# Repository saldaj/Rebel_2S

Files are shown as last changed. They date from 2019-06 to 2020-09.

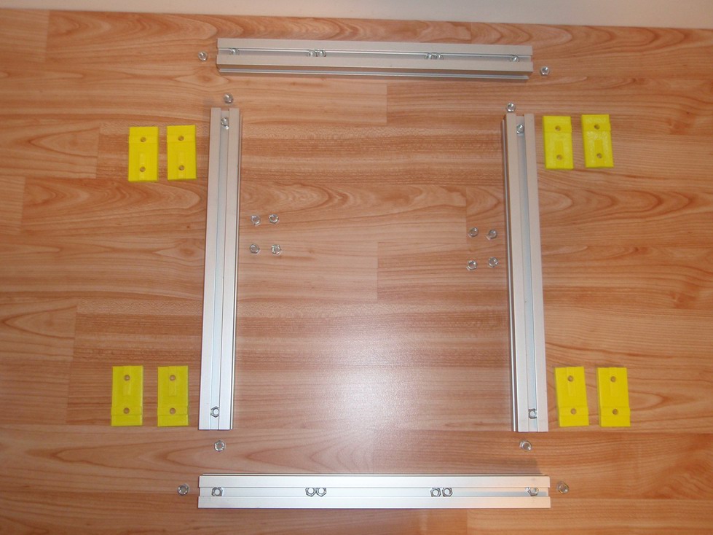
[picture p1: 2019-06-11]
Stavba/NavodyNaStavbu/rebel2-foto-montaz/001-priprava slozeni ramu.JPG

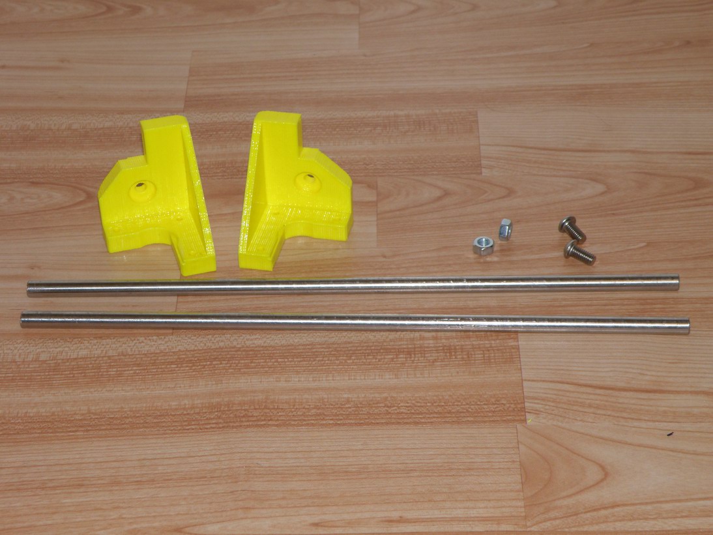
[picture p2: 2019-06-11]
Stavba/NavodyNaStavbu/rebel2-foto-montaz/018-priprava uchyceni Z motoru.JPG

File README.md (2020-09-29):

# Rebel_2S
This is the tracking place for build documents of one 3D printer - Based on the Rebel II printer

Jedna se o 3D tiskarnu Rebel II, ktera byla smontovana na zaklade dostupnych tipu a manualu. Vetsinu materialu se pokusim sem umistit, aby bylo vse pohromade.

Hlavni duvod proc toto vytvarim je FW - marlin, ktery jsem si musel upravit dle svych pozadavku, ale mezi verzemi jsem se zacal ztracet. Proto git je nejlepsi misto, kam dat FW aby byl trackovatelny hlavne vuci zmenam.

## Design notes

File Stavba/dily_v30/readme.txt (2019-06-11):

09:38 17/03/2015
k dispozici jsou dva totozne zdroje pro tisteni dilu:
A) Tistene dily rebel ii_v30_JRC
B) nebo \Stl_Tisk_v30\Sestavy_STL

- obe verze jsou aktualni.

tyto dve slozky se lisi par vecmi:
1. A) ma o 3 4 dily navic
	-Fan_mount_V5.4
	-Fan_mount_V8b
	-Full_g_LCD_vrchni
	-uchytkabelu.stl

2. B) ma moznost tisknout dily v sestave - uspora casu

Doporuèené minimální paranetry tisku:

- Steny/dna/vrchní výplne 1,2mm
- vnitrní výplne 25%

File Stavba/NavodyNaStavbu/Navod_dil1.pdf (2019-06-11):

## Postup stavby 3D tiskárny Rebel II

Martin Čihák – OK1UGA
Díl první - mechanika tiskárny.

Postup se týká stavby tiskárny Rebel II ze sady dílů zakoupené u Petra Zahradníka: http://www.clexpert.cz/3dtisk/rebel2/kompletni-sada-dilu
Je popisován postup který jsem použil při sestavení této tiskárny. V žádném případě netvrdím že je to postup jediný nebo nejlepší. Takto jsem to prostě udělal já a funguje to. Mě při stavbě velmi chyběl alespoň stručný návod a proto jsem ho napsal. Návod je napsán ve formě jednotlivých kroků kterými je potřeba při stavbě projít.
1. Vybalení hliníkových profilů
2. Vybalení pytlíku č. 3. Uvnitř je 52 matek. Ty je potřeba zbrousit asi o 0,3mm tak aby se vešly dovnitř profilů.
3. Nejkratší profily 320 mm jsou spodní boční, tedy vlevo a vpravo.
3.1. Do každého z nich nasadíte:
- zleva 2 matice doprostřed pro úhelník
- zprava 2 matice doprostřed pro úhelník
- nahoru 2 matice na každou stranu pro plastové vazby rohů
- dolu 2 matice na každou stranu pro plastové vazby rohů
To je tedy 2 profily krát 8 matic = 16 matic
3.2. Nejdelší profily 340 mm jsou přední, zadní a horní. Takže do těch spodních dvou nasadíte:
- nahoru 4 matice doprostřed pro držáky 8 mm vodících tyčí
- a nahoru ještě 2 matice na každou stranu pro plastové vazby rohů
- dolů 2 matice na každou stranu pro plastové vazby rohů
To je tedy 2 profily krát 8 matic = 16 matic
Tohle je tedy spodní část rámu, celkem 24 + 16 = 40 matic, tohle smontujete. Pak budete dělat svislé tyče.
3.3. Prostřední profily 330 mm jsou svislé, tam to bude takto:
- zleva 2 matice dolů pro úhelník
- zprava 2 matice dolů pro úhelník
- zpředu 1 matice dolů pro držák motoru
- zpředu 1 matice nahoru pro držák svislé tyče
- zezadu 1 matice nahoru pro vazbu rohů
To je tedy 2 profily krát 7 matic = 14 matic. Ale pozor, do levého svislého profilu zezadu přidejte ještě 2 matice doprostřed pro elektroniku. Celkem 16 matic.
3.4. Horní profil je zase ten nejdelší 340 mm a tam patří
- zpředu 2 matice na každou stranu pro vazbu rohů
- zezadu 2 matice na každou stranu pro vazbu rohů
To jsou celkem 4 matice. A jsme na těch 52 maticích.

Doporučuji do svislých profilů ještě přidat několik matic pro případné budoucí použití - např. pro držák zdroje a podobně. Tyto matky navíc ničemu nevadí a pokud bychom v budoucnu chtěli na tyto sloupky něco připevnit nemusíme rozebírat velkou část postavené tiskárny.

4. Vybalíme plastové díly z pytlíku č.4 - vazba rohů a smontujeme spodní rám. Šrouby na vazby rohů jsou v pytlíku č.5 - Vazba rohů.

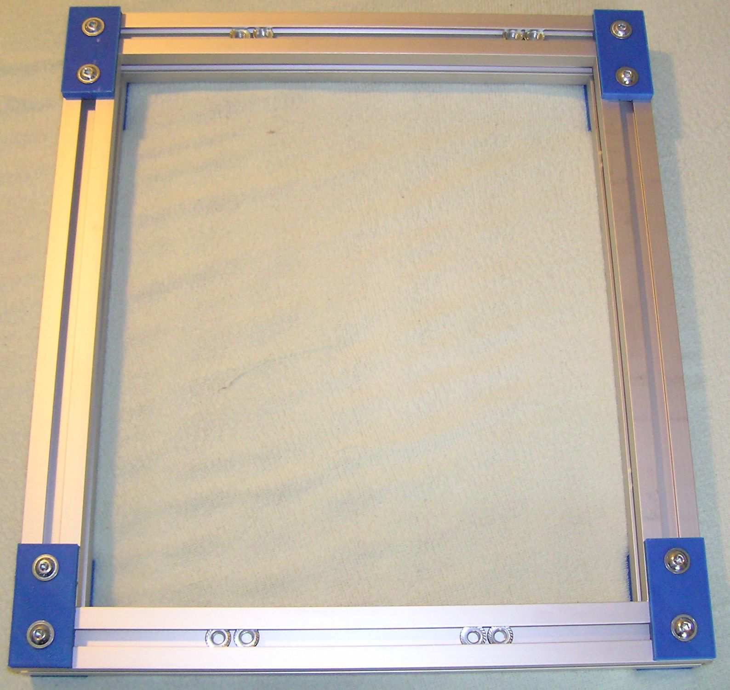
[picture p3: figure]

5. Sestavíme portál. Nejprve na svislé profily našroubujeme připevňovací úhelníky. Zatím utahujeme jen zlehka aby při manipulaci neupadly. Přišroubujeme horní profil. Zezadu je přišroubován posledními spojkami rohů, sepředu jsou profily spojeny držáky tyčí Z které jsou v pytlíku 20. K přišroubování použijeme šrouby z pytlíku 21. Do svislých profilů osadíme zbývající matky - viz odstavec 3.4 a sešroubovaný portál nasadíme na základní rám. Odměříme 100mm od zadní strany spodního rámu a v této poloze portál zlehka přitáhneme. Teď je dobré zkontrolovat pravý úhel mezi základním rámem a svislými profily. pokud je vše v pořádku přitáhněte upevňovací šrouby. Po zkontrolování pravého úhlu a vzdálenosti od konce je základní rám tiskárny sestavený.

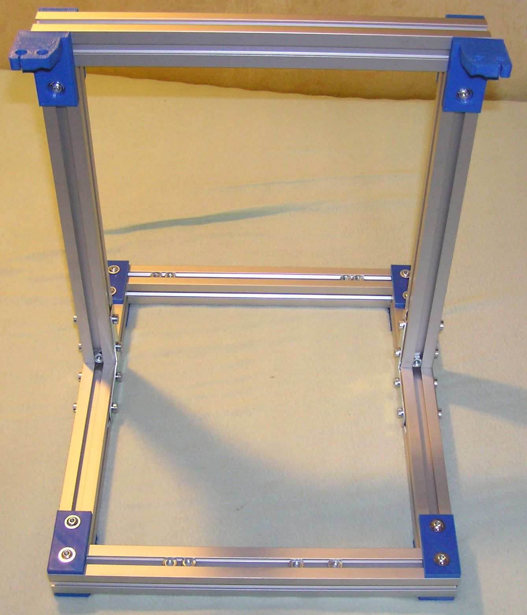
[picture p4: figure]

6. Pokračujeme montáží osy Y.

7. Vybalíme hliníkový stolek tiskárny z pytlíku 38. Z pytlíku 10 vybalíme držáky lineárních ložisek a nastrčíme do nich lineární ložiska z pytlíku 11. Sestavené držáky s ložisky přišroubujeme ke stolku. Našroubujeme z druhé strany kontramatky ale zatím neutahujeme. U držáků lineárních ložisek ale doporučuji nejprve zbrousit do roviny. případné nerovnosti dosedací plochy. Ty mohou způsobit při dotažení prohnutí držáků a vypadnutí ložiska.
8. Z pytlíku 30 vybalíme základnu držáku řemene osy Y a přišroubujeme ho na stolek šrouby z pytlíku 31. Další 2 díly z pytlíku 30 a zbytek šroubů si prozatím uložíme.

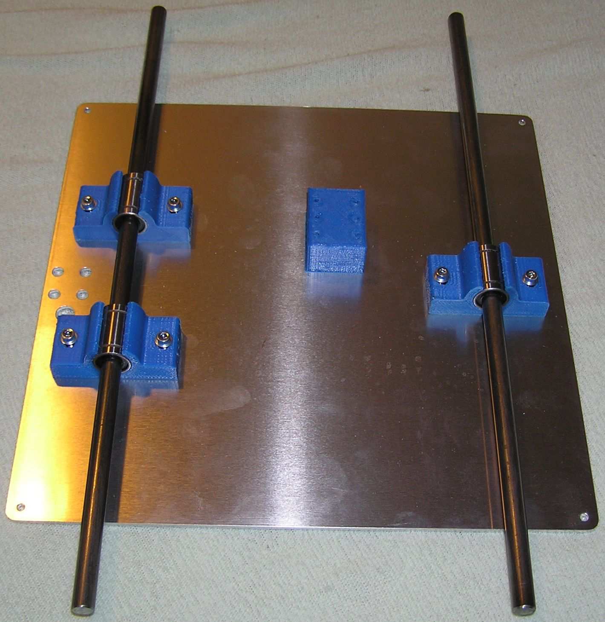
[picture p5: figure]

9. Vybalíme vodící a závitové tyče. Vybereme z nich vodící tyče osy Y - mají délku 365mm a nasuneme je do lineárních ložisek. Domky ložisek přitom jemně natočíme tak aby tyče v ložiscích hladce běhaly a byly rovnoběžné s hranou stolku. Rovnoběžnost kontrolujeme šuplérou.
10. Vybalíme 2kusy uchycení tyčí 8mm z pytlíčku č 6 a přišroubujeme je na předek základního rámu šrouby z pytlíku č.7. Zatím šrouby ale nebudeme dotahovat. Nastavíme vzdálenost předního pravého držáku tyče na 55mm od hrany rámu a utáhneme ho v této poloze. Vysuneme tyče z ložisek stolku a namažeme vnitřek ložisek přiloženým plastickým mazivem. Pak vrátíme tyče zpět do ložisek. Pravou tyč zasuneme do zafixovaného držáku a levý držák posuneme tak aby do něj šla zasunout levá tyč. Zezadu na tyče nasuneme zbývající 2 držáky a přichytíme je k rámu. Pravý zadní držák zafixujeme rovněž ve vzdálenosti 55mm od hrany rámu. Posunujeme stolkem dopředu a dozadu a 2 nezafixované držáky nastavíme do takové polohy aby stolek hladce klouzal po tyčích. Pak zafixujeme i tyto držáky.
11. Vybalíme Držák motoru osy Y z pytlíčku 22 a držák řemenice osy Y z pytlíku č.24 z pytlíčků 23 a 25 vezmeme matice a šrouby na připevnění držáků. Matice je potřeba opět před použitím zbrousit.

12. Do řemenice posuvu Y zamáčkneme ložiska a přišroubujeme ji do držáku řemenice. Otvory pro ložiska bylo nutné převrtat na správný průměr 10mm. Řemenice se musí na
šroubu který tvoří osu volně protáčet.
13. Dále budeme pokračovat posuvem Z a současně X.
14. Vybalíme držáky motorů osy Z z pytlíku 8. a přišroubujeme je šrouby z pytlíku 9 na svislé profily.

### 15. Vybalíme pojezd osy Z levý z

pytlíku 12. Z pytlíku 13
vyjmeme 2 lineární ložiska a namáčkneme je do vidícího
otvoru v plastovém dílu. Do připravené osmihranné díry teplem páječky zamáčkneme
mosaznou posuvovou matku.
Ujistěte se, že je matka zatavená rovně nejlépe opatrným

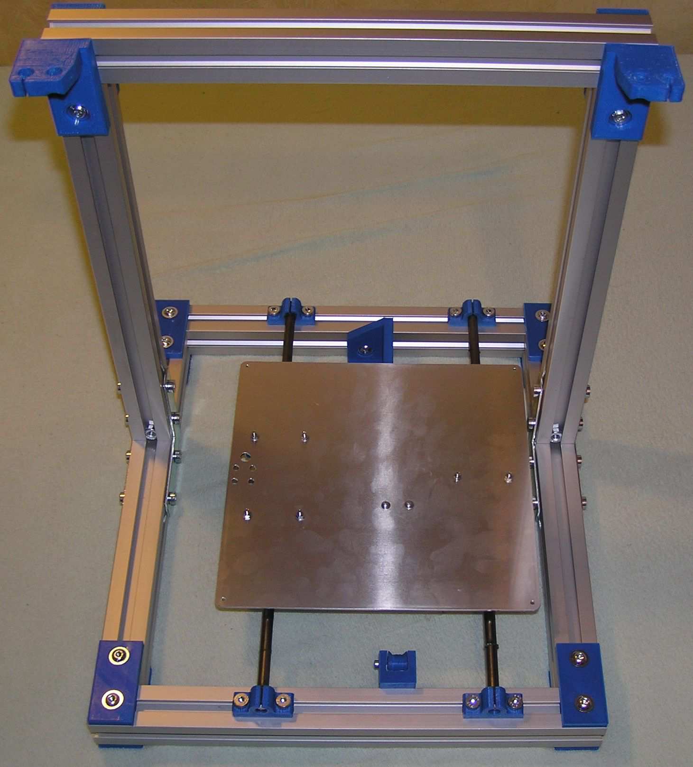
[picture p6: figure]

zašroubováním závitové tyče a kontrolou jejího vedení. Zde jsem si dovolil malou modifikaci. Zdálo se mi, že matice není dostatečně jištěná proti vytržení ze svého lože. Jedna z matic se dokonce lehce viklala. Proto jsem se rozhodl pojistit. Z ABS filamentu jsem vyrobil kroužek a zamáčkl ho do lože nad maticí a zalepil ho lepidlem vyrobeným rozpuštěním ABS filamentu v Acetonu. Tak je matice bezpečně zajištěna ve svém pouzdru a nemusím se obávat jejího vytržení. Pozor! Pan Zahradník

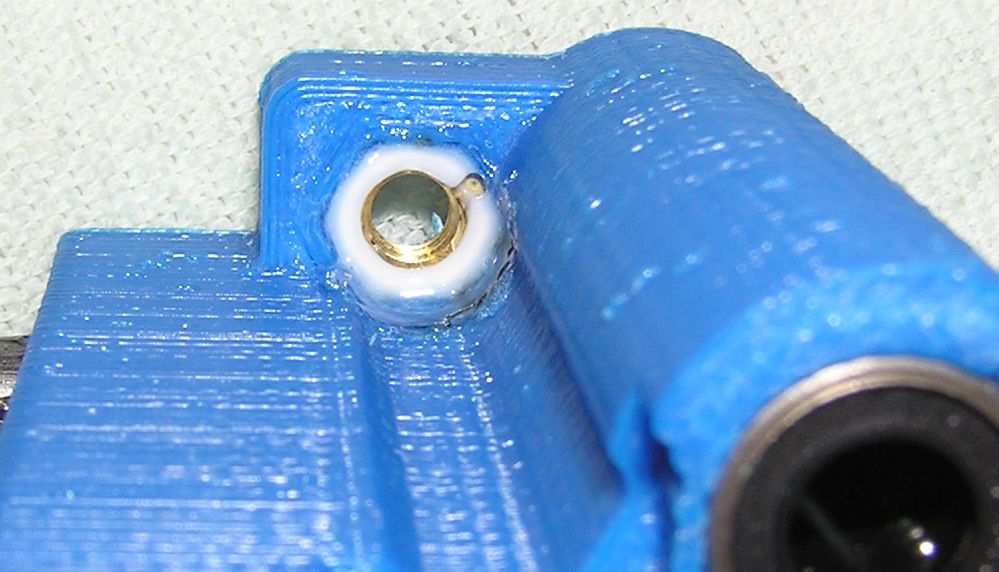
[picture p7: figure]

mě upozornil, že můj postup v tomto bodě není správný. On matici do jejího lože lisuje za studena a matice pak prý krásně dosedne na dno svého lože a je tak je přesně usazena ve správné poloze. S tím souhlasím. Mě se zdálo že je přesah matice vůči otvoru příliš velký a proto jsem použil zalisování za tepla. Obával jsem se roztržení plastového dílu.
16. Vyjmeme z pytlíčku č. 14 Pravý posuv osy Z a nastrčíme do něj lineární ložiska z pytlíku. Dále zatavíme do připraveného osmihraného otvoru mosaznou posuvovou matici. Opět jsem použil stejnou modifikaci jako v předchozím bodě. Do řemenice natlačíme 2 ložiska a přišroubujeme ji do otvoru v platovém dílu pravého posuvu Z.
17. Protáhneme díry pro posuvové tyče obou pojezdů osy Z frézou o průměru 8mm. Tyče by měly jít zastrčit lehkým tlakem. Pak nastrčíme posuvové tyče osy X délky 315mm do levého pojezdu ozy Z.
18. Z pytlíku 16 vybalíme největší díl pojezdu extruderu. Do něj namáčkneme 3 axiální ložiska z pytlíku č.17. Začistíme plochy pro vložení extruderu tak aby do nich extruder hladce zapadl. Vložíme extruder a zatlačíme k němu upevňovací díl. Přišroubovávat ho zatím nebudeme. Odstřihneme kus plastového filamentu a otvorem pro vstup filamentu v plastovém dílu ho prostrčíme dovnitř extruderu a protáhneme ho extruderem (Bez nasazené trysky). Filament musí hladce procházet bez jakéhokoliv drhnutí nebo narážení do vyosených dílů. Pokud vše funguje jak má extruder vyjmeme a uložíme ho zatím zpět do krabičky ve které jsme ho dostali.
19. Z pytlíku č.17 vyjmeme držák kladky a vložíme do něj ložisko, které slouží jako kladka proti zubatici a přišroubujeme ho do držáku. Vezmeme plastový díl sloužící jako držák pružiny a do otvoru pro matku na dně vybrání pro pružinu vložíme matku a z druhé strany ji přišroubujeme šroubem který slouží pro nastavení přítlaku. Na jeden konec pružiny nasadíme kolečko s osazením. Vložíme pružinu a nastrčíme ji plastovým kolečkem na nastavovací šroub. Otáčením tohoto šroubu pak můžeme řídit přítlak pružiny. Na motor nasuneme zubatici a motor nasuneme do pozice ve které má být upevněn v pojezdu. vložíme i rameno s kladkou a držák pružiny do správných pozicí. Nejprve motor zlehka chytneme dvěma spodními šrouby a pak zašroubujeme i horní dva šrouby. Vložíme extruder a zajistíme ho držákem extruderu. Zvrchu prostrčíme kousek filamentu mezi kladku a zubatici a nastrčíme ho do extruderu. Motor ve spodním uchycení posuneme tak, aby byla zubatice ve správné poloze a spodní dva šrouby utáhneme. posuvem filamentu pootočíme zubatici tak aby pojistný červík byl proti nám. Zubatici na ose motoru posuneme tak aby správně zapadla do filamentu a utáhneme červíkem. Filament musí jít celým sestaveným dílem
hladce bez zadrhávání
nebo prohýbání mezi
kladkou a zubaticí. Pokud
je vše v pořádku utáhneme
všechny šrouby kromě
toho, který drží ramínko s kladkou které musí zůstat
pohyblivé. Pro další
montáž vyjmeme extruder
abychom si ho při dalších
pracích nepoškodili. Pozor při utahování šroubů. Mají malou hlavu a při

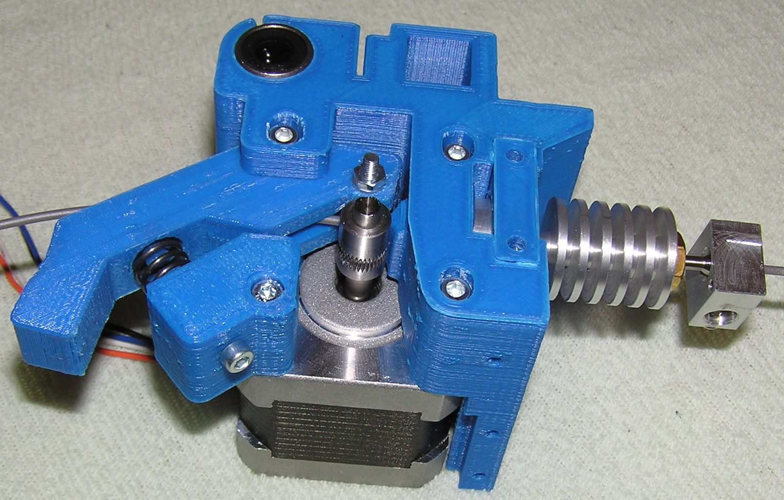
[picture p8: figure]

necitlivém utahování se snadno zavrtají do plastu.
20. Namažeme lineární ložiska pojezdu extruderu plastickým mazivem. Pak sestavený unašeč extruderu nasuneme na posuvové tyče posuvu X. Na pravou stranu posuvových tyčí nasuneme pravý pojezd osy Z.
21. Do levého pojezdu Z přišroubujeme motor. Prozatím jen pravými kratšími šrouby. Na osu motoru nasuneme a zlehka přitáhneme červíkem
řemenici.

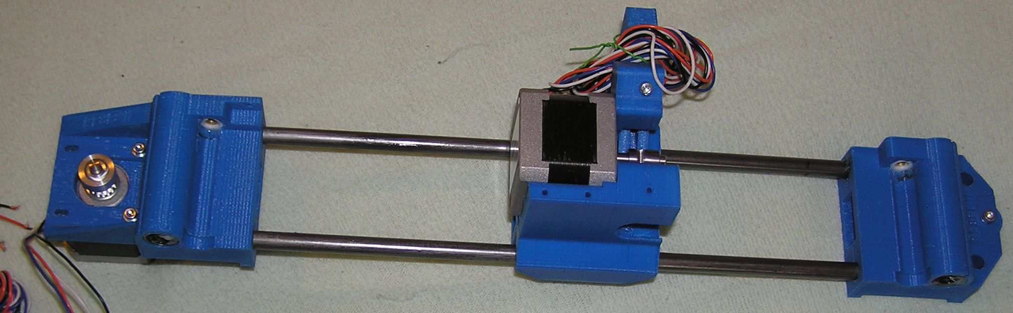
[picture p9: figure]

22. Vezmeme tyče svislého posuvu a na zkoušku je nasuneme do vodících otvorů. Držáky motorů svislého posuvu posuneme o několik milimetrů nad základní rám tak aby horní konce tyčí vyplňovaly celou tloušťku horních vodících plastových dílů. V této poloze držáky motorů svislého posuvu dotáhneme. Pak vyjmeme tyče ven z vodítek.
23. Namažeme lineární ložiska svislého posuvu vazelínou. Do levého vedení shora nasuneme vodící tyč. Z balíčku s pomůckami vyjmeme suchý zip a připravíme si ho k použití. Vezmeme sestavený posuv a nasadíme ho na připravenou tyč. Pojezdem vyjedeme po tyči až nahoru a zajistíme v horní poloze suchým zipem. Pak zasuneme vodící tyč až do spodního vodícího
otvoru z držáku motoru.
Nasuneme i pravou
vodící tyč a ukotvíme ji
ve spodním vodícím
otvoru v pravém držáku
motoru.
24. Odstraníme suchý zip a zkusíme zda jde svislým
posuvem volně
posouvat po vodících
tyčích.
25. Pokud je vše v pořádku můžeme pokračovat
montáží závitových tyčí.
Na hřídele obou motorů
nasadíme spojky mezi
hřídelí a závitovou tyčí
a přitáhneme je červíky.
Suchým zipem si
sestavenou osu X
zajistíme v takové
poloze aby plastové díly
zůstaly těsně nad
nasazenými spojkami.
Seshora našroubujeme
závitové tyče až do

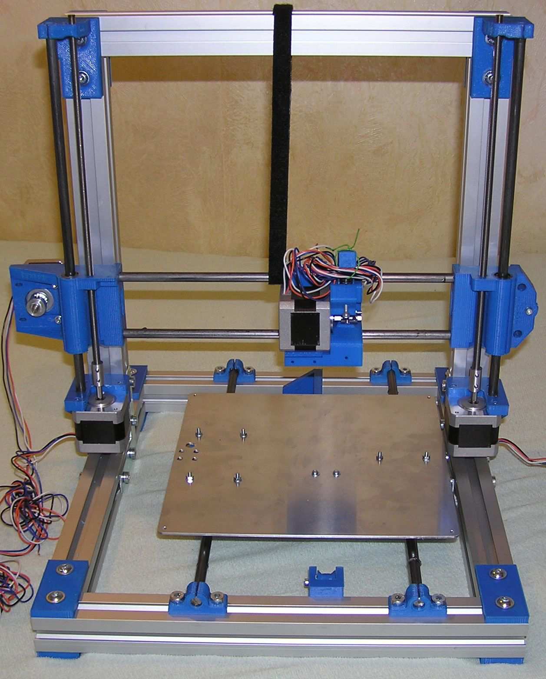
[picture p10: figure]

spojek. Ve spojce je našroubujeme až na doraz a přitáhneme červíkem. Pak závitové tyče jemně potřeme vazelínou pro hladký chod. Odstraníme suchý zip a můžeme ho použít třeba pro provizorní zajištění volných vodičů od motorů.
26. Změříme vzdálenost spodních hran plastových unašečů svislého posuvu od držáků motorů a otáčením hřídelí motorů nastavíme stejnou vzdálenost.
27. Motor osy X zlehka povolíme a v protáhlých dírách pro šrouby ho posuneme do pravé krajní polohy. Z pytlíku s gumovými součástmi vyjmeme ozubený řemen. Jeden konec upevníme v zakončení řemenu na zadní straně pojezdu extruderu pomocí těsnící vložky. Pak řemen protáhneme celou dráhou řemene až na druhou stranu

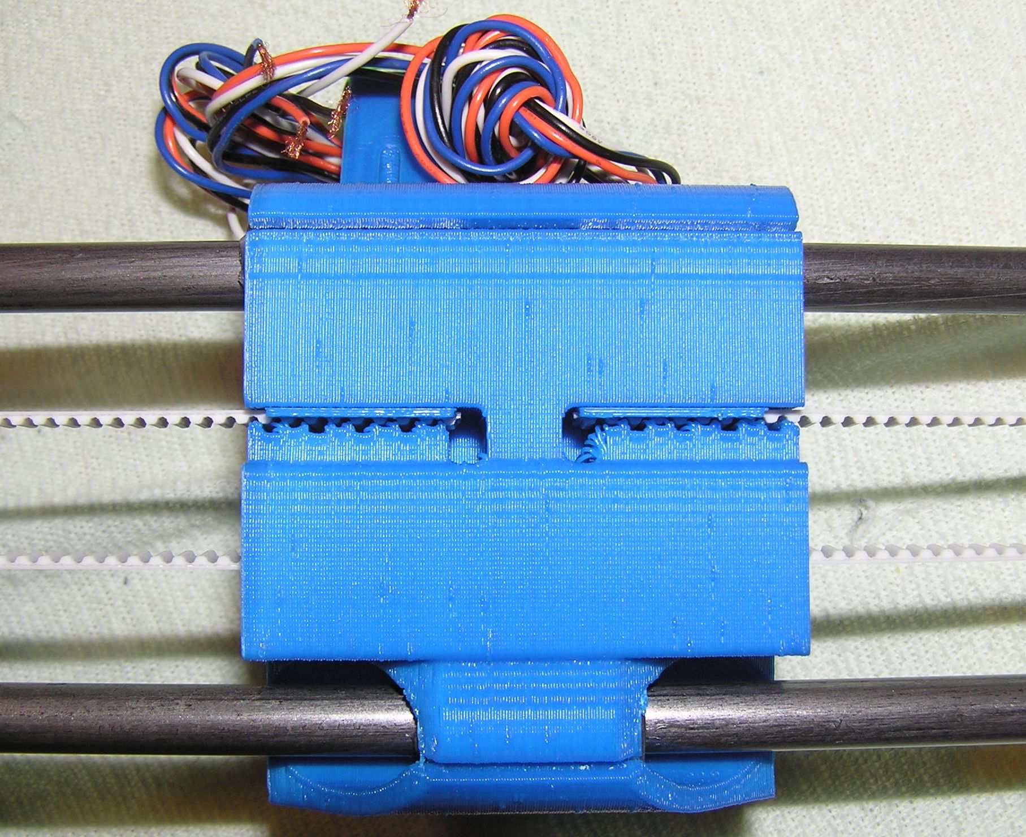
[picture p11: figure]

pojezdu extruderu. Řemen zlehka vypneme, naměříme jeho délku a potřebný kus ustřihneme. Řemen napneme a nasuneme i s těsnící vložkou do uchycení řemene na druhé straně pojezdu extruderu. Vypnutí řemene zajistíme posunutím motoru doleva a dotažením upevňovacích šroubů.
28. Protáčením osy motoru vyzkoušíme posuv osy x. Musí jít snadno a lehce.
29. Pokračovat budeme pohonem stolku. Vybalíme poslední motor a přišroubujeme ho do držáku motoru šrouby z pytlíku č.23. Motorem jde v podélných dírách pro šrouby pohybovat dopředu a dozadu. Šrouby zatím dotáhneme jen zlehka a motor popotáhneme co nejvíc dopředu. Nasadíme řemenici na osu a odměříme střed plastové řemenice na předním úhelníku od kraje stolku. Na stejnou vzdálenost nastavíme i řemenici motoru a přitáhneme oběma červíky.
30. Vezmeme zbytek ozubeného řemene a upevníme ho jedním koncem do držáku řemene na spodní straně stolku úchytkami z pytlíku č.30. Řemen protáhneme přes řemenici motoru a kladku na přední straně rámu a přivedeme ho zpět k držáku řemene. Zde řemen zlehka vypneme a utáhneme. Pak popotažením motoru vypneme řemen a motor utáhneme.
31. Tím je hlavní práce na mechanické konstrukci tiskárny hotová. Zbývá jen několik dodělávek.
32. Na levé straně pojezdu svislé osy přišroubujeme
držák kabeláže pomocí
zbývajících dvou šroubů
uchycení motoru osy X.
Dále pak na horní část
přišroubujeme mikrospínač
který slouží jako koncový
spínač. Unašečem Extruderu najedeme do levé krajní
polohy a ověříme že
mikrospínač spíná.
33. Na přední část vozíku
extruderu přišroubujeme
držák ventilátoru a kabeláže z pytlíku č.18 šrouby z

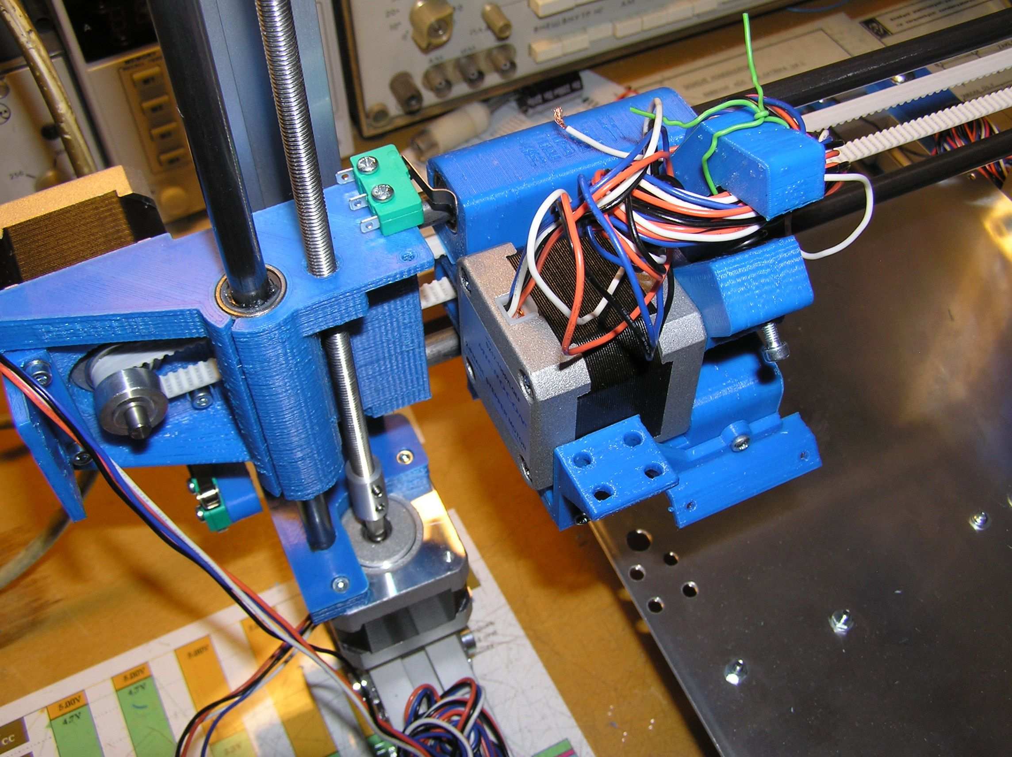
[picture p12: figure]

pytlíku č.19. Ventilátor si zatím necháme bokem.
34. Na zadní profil nahoru přišroubujte držák koncového spínače osy Y z pytlíku č.26 šroubem z pytlíku č.27. Matku M5 do drážky lze nasunout zvenku skrz drážku - není nutné ji tam mít vloženou předem. Dále na tento držák přišroubujte mikrospínač. Pojezdem stolku do zadní polohy si ověřte, že spínač v krajní poloze spíná.
35. Vybalíme držák koncového spínače svislé osy z pytlíku č. 28. Do šestihranného otvoru v pružném raménku vložíme matičku a
našroubujeme dovnitř stavěcí šroub. Na pružné raménko z boku
přišroubujeme mikrospínač a celý

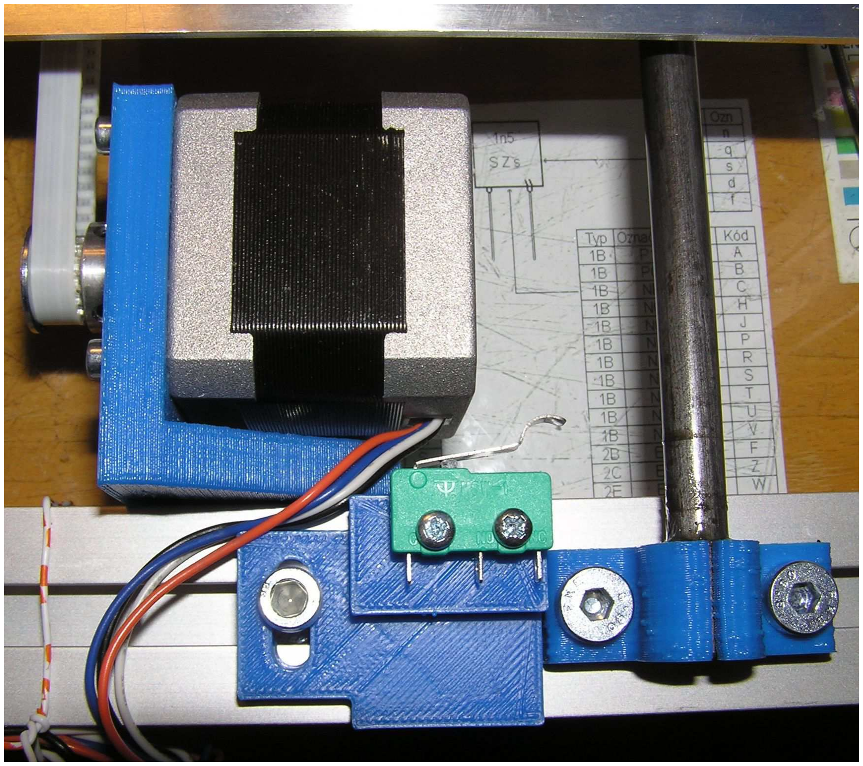
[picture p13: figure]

díl přišroubujeme na bok tiskárny. do přibližné polohy kterou odhadneme. Přesnou polohu nastavíme při oživování tiskárny. Matku M5 do drážky lze nasunout zvenku skrz drážku - není nutné ji tam mít vloženou předem.
36. Na levý svislý profil zezadu přišroubujeme držák elektroniky z pytlíku 36 šrouby z pytlíku 37.
37. Na vrchní profil přišroubujeme držáky filamentu.

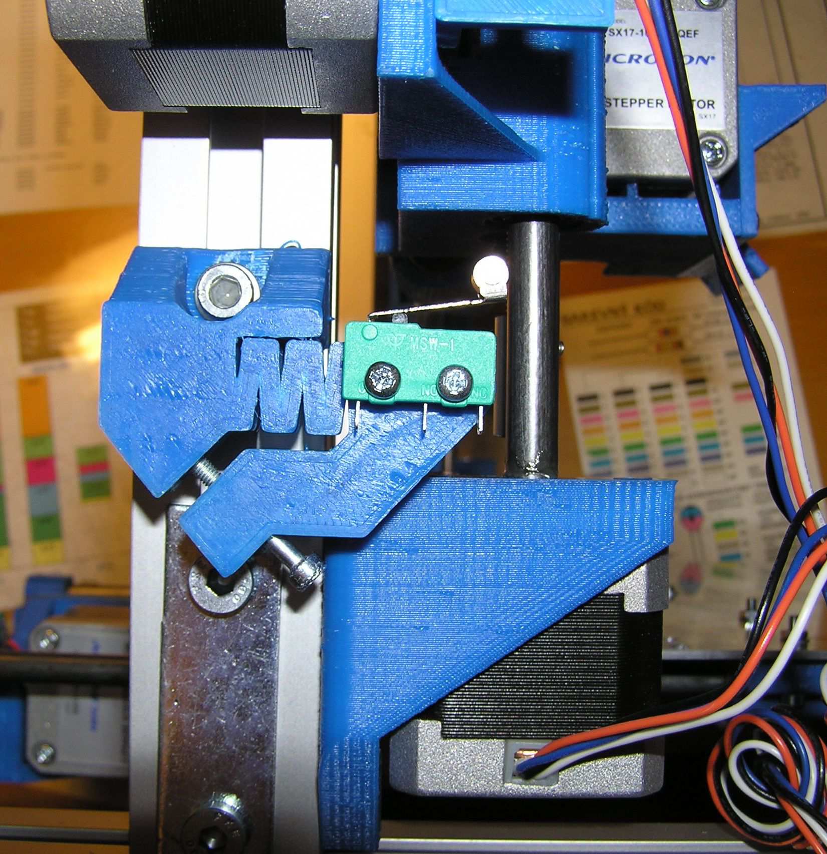
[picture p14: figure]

Tím je mechanická část stavby tiskárny hotová. Pokračovat budeme zapojením elektrických částí tiskárny v dalším souboru.

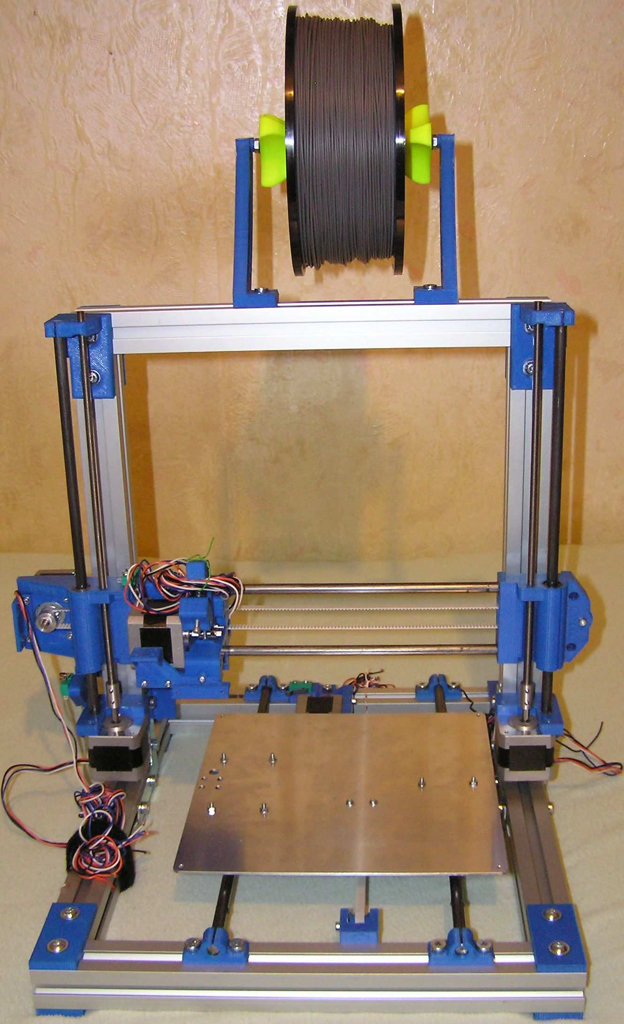
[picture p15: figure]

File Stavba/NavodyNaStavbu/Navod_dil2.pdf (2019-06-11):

## Postup stavby 3D tiskárny Rebel 2

Martin Čihák – OK1UGA
Díl druhý - elektronika tiskárny.

Celá tiskárna je řízena procesorovou deskou Arduino Mega 2560. Na procesorovou desku je nasazena rozšiřující deska RAMPS v. 1.4. A na této desce jsou ještě navíc nasazeny drivery jednotlivých krokových motorů. Všechna elektrická zařízení tiskárny jsou připojena k desce RAMPS. Bohužel je deska RAMPS levný čínský výrobek a proto si ji musíme upravit tak aby bez problémů fungovala a snesla požadavky na ni kladené.

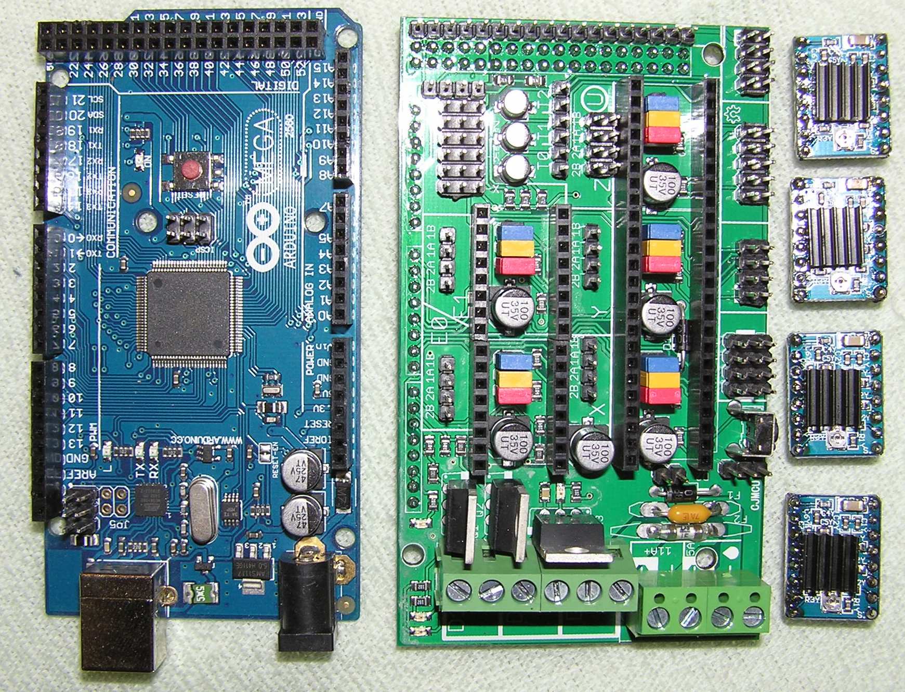
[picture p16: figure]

Tento popis je napsán formou postupných kroků, které by měly být provedeny abychom zprovoznili elektroniku tiskárny.

Můj postup rozhodně není jediný možný a ani nemusí být nejlepší či nejvýhodnější. Je to prostě postup který jsem použil já při výrobě mé tiskárny.

1. Výrobu začneme úpravami desky RAMPS. Petr Zahradník v informačním mailu posílá obrázek na kterém je znázorněno zapojení desky. Vše se bude zapojovat podle tohoto obrázku.
2. Nejprve musíme vyměnit nevhodné součástky. Potřebné součástky najdeme v pytlíku č. 51 ( elektronika ). Musíme vyjmout a vyměnit FET který má vysoké Rdson a při průtoku proudu topení stolku se přehřívá. V pytlíku se součástkami najdeme kvalitní FET, který procházející proud bez problémů snese. Dále vyměníme 2 pojistky. S původními pojistkami jsou značné problémy a proto je nahradíme tavnými pojistkami z pytlíku. Další problémy jsou s ohřívající se svorkovnicí pro přívod napájecích napětí. Proto ji rovněž vyměníme za dodanou svorkovnici.

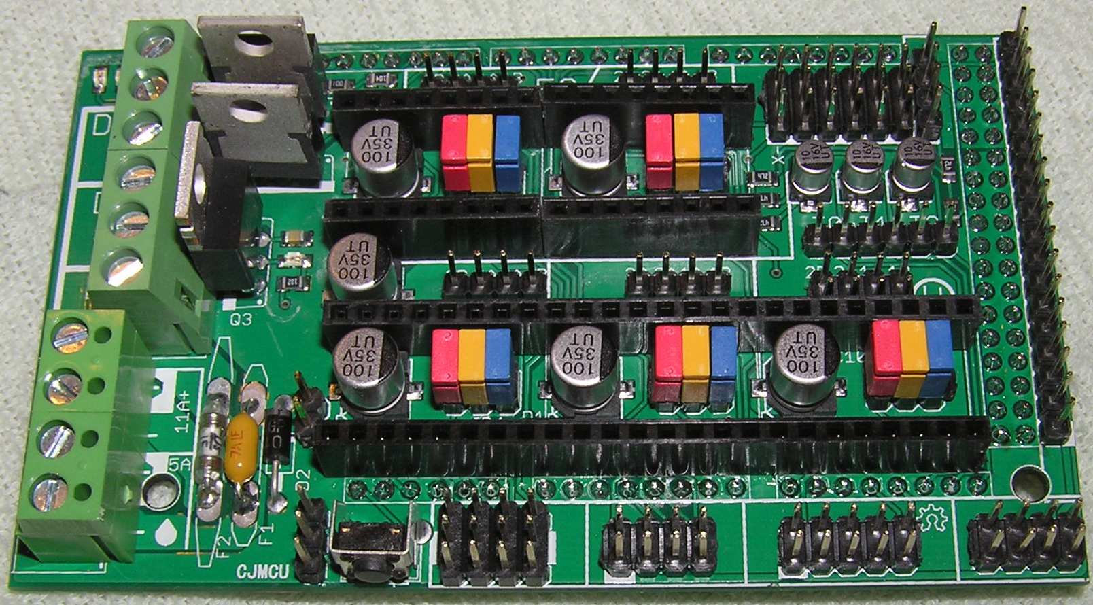
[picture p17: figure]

3. Pokud používáme celokovový extruder musíte ho trvale chladit. Proto osadíme konektor mezi pojistkami a spodním levým elektrolytickým kondenzátorem. Dále osadíme diodu D1 pod prostředním spodním kondenzátorem. Poslední úprava je posíleni spojů na DPS od svorkovnice 12V ke svorkovnici pro vyhřívání stolku a dál k FET tranzistoru který spíná topení stolku . Tyto spoje jsou příliš tenké a ohřívají se. Posílil jsem je kusem drátu připájeným paralelně k těmto spojům.
4. Dalším krokem bude připájení konektorů do destiček driverů. Konektory se do desky nastrčí ze strany popisů, pájejí se na straně součástek. Aby byla dodržena kolmost konektorů je nejjednodušší nasadit konektory na kraj zásuvek v desce RAMPS a rychle připájet krajní piny. Pak destičku driveru z RAMPsu vyjmeme a zapájíme zbytek. Když máme destičky hotové ještě na všech přilepíme k driveru dodané chladiče. Přilepíme je s takovou orientací aby žebra byla na tiskárně orientována svisle.
5. Na držák elektroniky přišroubujeme Arduino a nasuneme na něj desku Ramps. Do desky Ramps pak nasuneme destičky driverů. Drivery jsou choulostivá zařízení. Proto je nutné zde upozornit na některé zásady které je nutné dodržet pokud mají naše snažení ve zdraví přežít.
5.1. Nastavování napětí trimrem na driveru se nesmí dělat ve chvíli kdy motor běží ale pouze v klidovém stavu.
5.2. Připojovat nebo odpojovat motory lze pouze když je celé zařízení vypnuté. Napěťové špičky vzniklé připojením / odpojením by mohly zničit drivery.
5.3. Pokud jsou motory připojené nesmíme ručně pohybovat posuvy aby napětí indukované motory nezničilo drivery.
5.4. Konektory kterými jsou motory připojené musí být kvalitně nakrimpované. Pokud by zde byl špatný kontakt dopadlo by to stejně jako v bodě 5.2.
6. Z pytlíku č. 38 vyjmeme desku ohřevu stolku a připájíme k ní tlusté vodiče se silikonovou isolací. Pozor! Veškeré práce na desce ohřevu provádíme pouze ze spodní strany. To je strana kde je patrný vyleptaný topný meandr. Hladkost horní strany nesmí být ničím narušena jinak by na ní nesedělo krycí sklo. Jeden vodič připájíme na PIN 1 a jedním koncem druhého vodiče spojíme PINy 2 a 3. Můžeme překontrolovat odpor takto připravené desky. Já naměřil 0,74Ω. To by znamenalo, že při napájení 12V deska bere něco přes 16A. Nesmíme ale zapomenout na další odpory v obvodu od zdroje na desce s RAMPS, přívodní vodiče a zvýšení odporu topné desky po zvýšení teploty. Nakonec by tedy celkový proud neměl překročit 15A
7. Pokračujeme instalací termistoru do desky ohřevu. Vyjmeme ho z pytlíčku č. 46 (Termistory). Jeho vývody zkrátíme přibližně na 1cm a připájíme na ně přívodní vodiče s teflonovou isolací. pak přes spoje přetáhneme přiložené isolační bužírky. Dírku uprostřed topné desky z horní strany přelepíme kouskem kaptonové pásky. Zespoda pak do ní mázneme malé množství teplovodivé vazelíny a vložíme do ní termistor. pak termistor zajistíme přelepením kaptonovou páskou a přilepíme jí i přívodní vodiče k desce na mnoha místech. Nešetřete zde páskou. Nechceme aby termistor za provozu vypadl. To by patrně vedlo ke zničení topné desky.

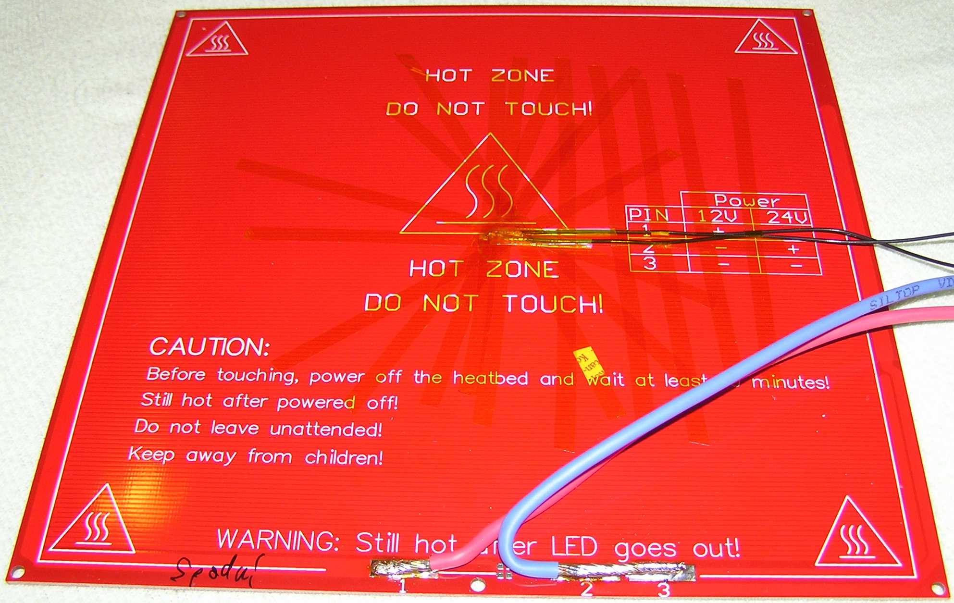
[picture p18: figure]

8. V dalším kroku připevníme topnou desku na stolek. Ze spodní strany do všech rohů stolku nastrčíme dlouhé šrouby z pytlíku č. 33 (distanc stolku) a přitáhneme je matičkami. Z

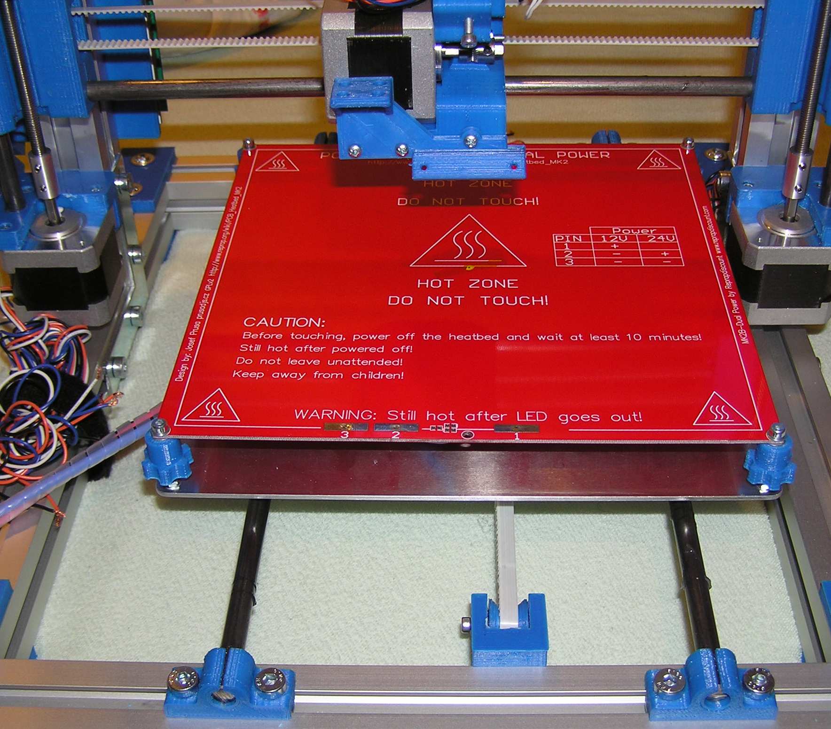
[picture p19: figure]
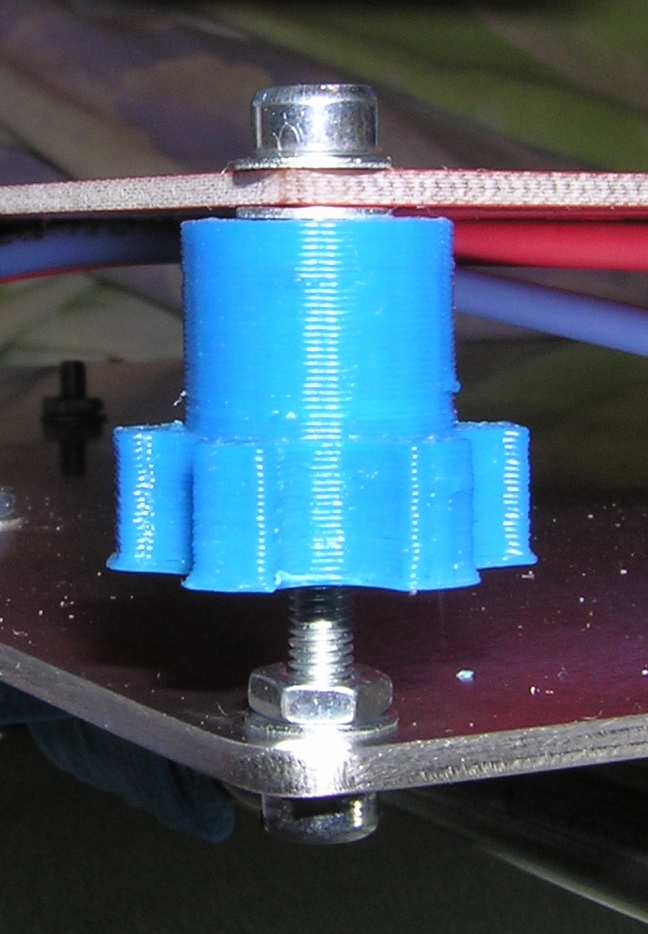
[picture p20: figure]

vrchu na ně našroubujeme plastové kolečka z pytlíku č. 32. Vývody od topné desky protáhneme větší dírou ve stolku. Stolek položíme na plastová kolečka a přišroubujeme ho do nich kratšími šroubky. Z horní i dolní strany topné desky dáváme podložky aby se v nich šroubek snadněji protáčel. Plastová kolečka slouží pro přesné nastavení výšky stolku. Přiznám se ale poctivě že se mi tato konstrukce nelíbí a patrně to bude jedna z prvních věcí kterou na své tiskárně udělám jinak. Kabely které procházejí stolkem na spodní straně přitáhneme ke stolku pomocí dvou stahovacích pásků které procházejí čtyřmi menšími dírami ve stolku. Na kabel namotáme spirálovou bužírku tak aby chránila celou délku pohyblivé části kabelu. Ale na fotografii je to udělané špatně. Spirálová bužírka má být přitažena pod pásky. Po vyfocení když jsem si uvědomil chybu jsem to musel předělat

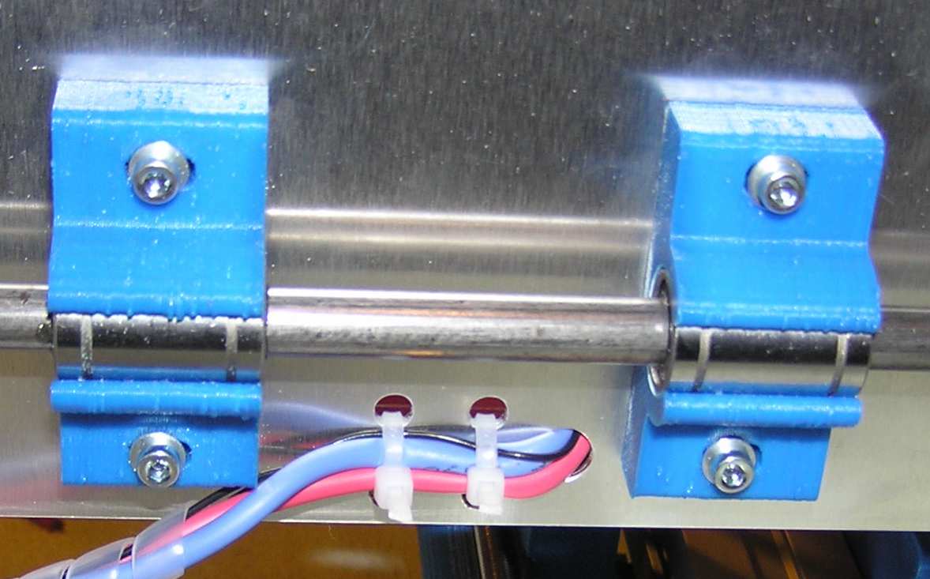
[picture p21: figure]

9. Pokračovat budeme extruderem. Nejprve na spodní konec extruderu našroubujeme trysku a pevně utáhneme klíčem. Pro první pokusy jsem zvolil trysku o průměru 0,5mm. Pak do většího otvoru vložíme topný odpor a zajistíme ho šroubky. Na vývody termistoru navlékneme připravené teflonové bužírky a zkrátíme je na takovou délku abychom na konci vývodů termistoru měli dostatečnou délku obnažených vývodů pro připájení vodičů. Pozor - nezkracujte vývody termistoru ale pájejte až na konci. Pokud bychom pájeli těsně u topného tělesa vysoká teplota by mohla částečně natavit cín. Proto pájíme až na konci vývodů termistoru, kde teplota zdaleka nebude tak vysoká. Připravený termistor s isolačními bužírkami prostrčíme otvorem v topném tělese. Dejte přitom pozor aby termistor byl uprostřed hliníkové kostky a teflonové bužírky musí doléhat až k pouzdru termistoru. Pak vývody ohneme tak, aby se termistor již nemohl v hliníkové kostce pohybovat. Do díry kolem termistoru natlačíme teplovodivou vazelinu a pak v této poloze vývody zajistíme
kaptonovou
páskou.
Neomotejte
páskou ocelový
krček mezi
chladičem a
hliníkovou
kostkou. Ten se
musí chladit a
páskou bychom
bránili odvodu
tepla. Na konce
vývodů termistoru
připájíme vodiče s
teflonovou isolací
spoje převlékneme

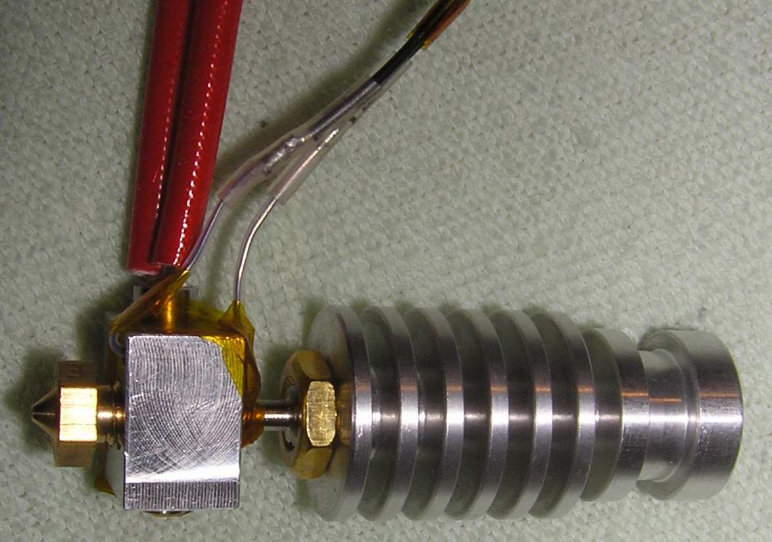
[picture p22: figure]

silikonovou bužírkou nebo zaizolujeme opět kaptonovou páskou. Vývody pak ohneme nahoru, kde budou ofukovány ventilátorem který chladí extruder. Pro jistotu bychom měli zkontrolovat ohmetrem připojení odpor termistoru a ověřit že některý vývod nemá zkrat na hliníkovou kostku. Topné těleso má odpor přibližně 8Ω a termistor při pokojové teplotě okolo 100kΩ.

10. Přišroubujeme ventilátor z pytlíku č. 19. do držáku na extruderu. Přívody ventilátoru jsou opatřeny konektorem. Konektor ustřihneme a na červený a černý drát připájíme přiloženou dvojlinku. spoje převlékneme smršťovací bužírkou a celý spoj převlékneme dalším kusem tlustší smršťovací bužírky. Žlutý drát nepotřebujeme a proto ho ustřihneme těsně u telesa ventilátoru. Ventilátor vyzkoušíme připojením konců vodičů na zdroj 12V.

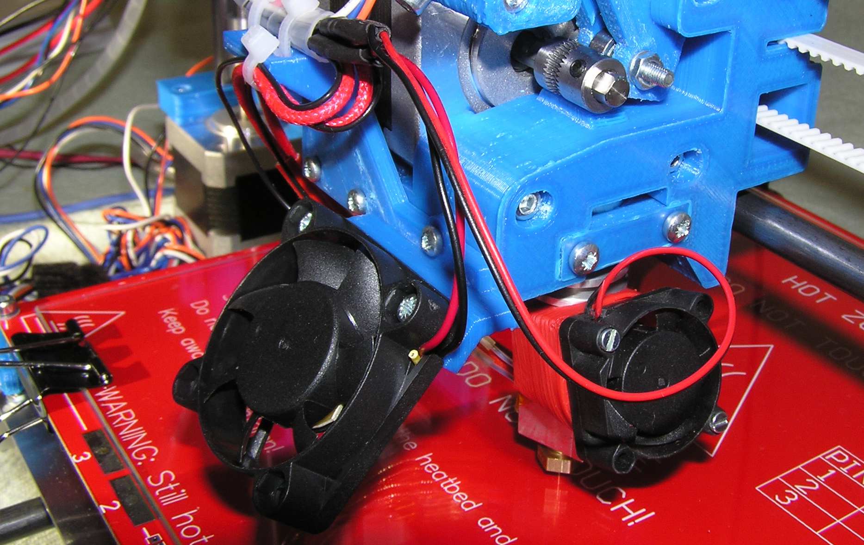
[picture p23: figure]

11. Dále zkompletujeme chlazení extruderu. Z krabičky od extruderu vyjmeme miniaturní ventilátor a přišroubujeme ho dvěma šrouby k plastovému dílu. Ustřihneme konektor na konci vývodů ventilátoru a připájíme na ně dvojlinku. Zde jsem použil dvojlinku jiné barvy než je přiložená aby nedošlo k záměně s dvojlinkou od ventilátoru který jsme připojili v předchozím bodě. Ale není to nutné. Ventilátor opět vyzkoušíme připojením konců vodičů na zdroj 12V. Pokud je funkční, nasadíme ventilátor plastovou armaturou na chladič extruderu.

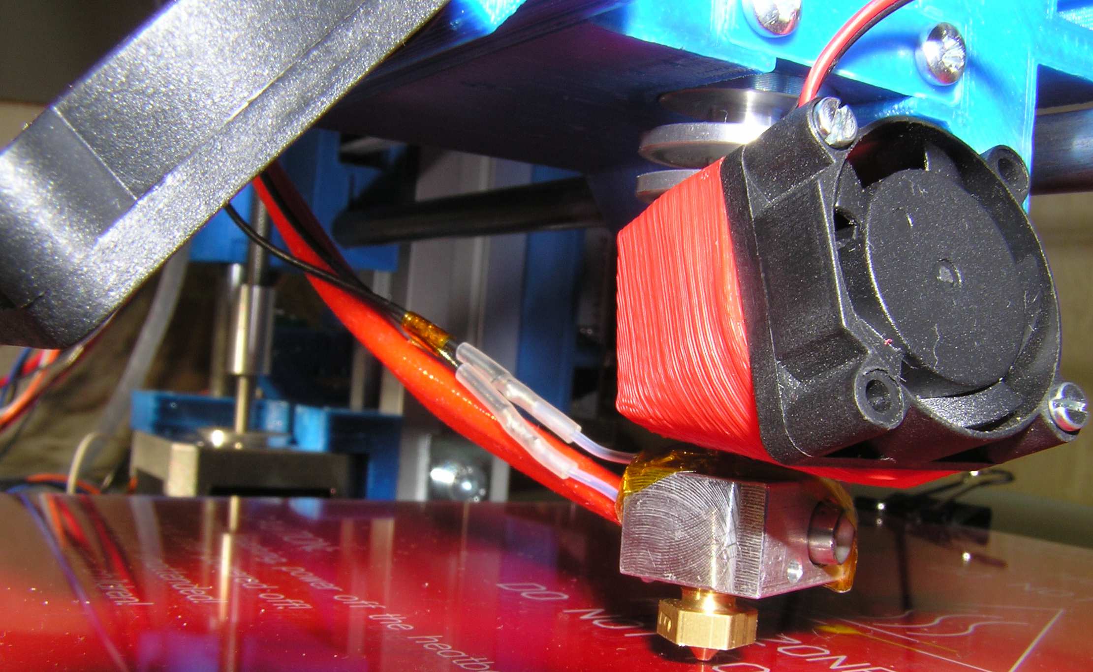
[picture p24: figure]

12. Tím máme osazenou kompletní elektrickou výzbroj vozíku extruderu a můžeme vodiče vedoucí od vozíku svázat spirálovou bužírkou v potřebné délce tak aby svázaný úsek vodičů vyšel od nejvzdálenějšího místa, kde vozík extruderu bude k držáku kabeláže na držáku motoru posuvu Y. Svazek si provizorně přichytíme na držák kabeláže vedle motoru posuvu Y.
13. Natáhneme vývody motoru extruderu a zakrátime je tak aby byly stejně dlouhé. Pak na ně nakrimpujeme konektory a nastrkáme je do plastových dutinek v pořadí barev zleva Modrá, bílá, oranžová, černá. Stejné pravidlo budeme dodržovat i u ostatních motorů. Doporučuji hned jednotlivé konektory označovat aby později nedošlo k záměně. Když budou připojovací vodiče ve svazku už nemáme možnost poznat který patří ke kterému motoru.

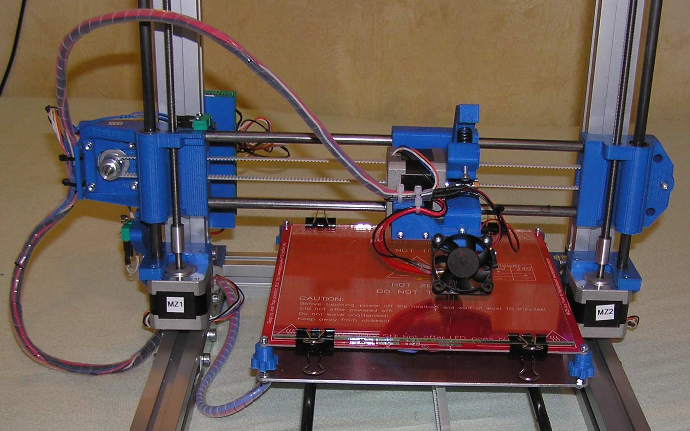
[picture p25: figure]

14. Naměříme vodiče a nakrimpujeme i vývody ostatních motorů. Vývody od pravého motoru svislé osy jsem protáhl středem zadního hliníkového profilu.
15. Natáhneme vodiče od koncových spínačů. Já jsem koncové spínače připojil na 2mm fastony ale je možné je i připájet. Fastony jsem zaizoloval smršťovací bužírkou. Připojujeme krajní vývody mikrospínačů. V klidové poloze mají být sepnuté.

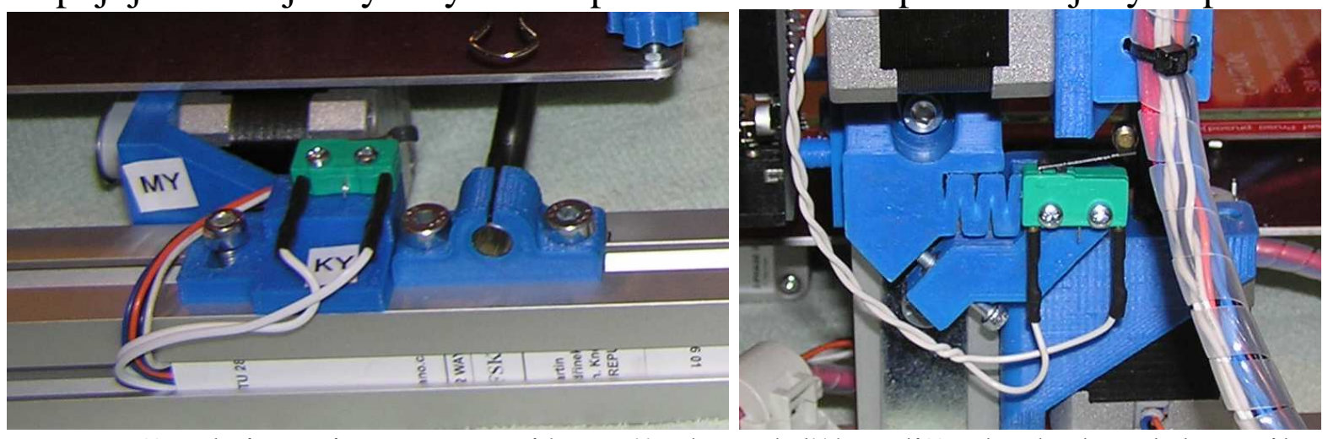
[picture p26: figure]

16. Postupně nakrimpujeme a zapojíme všechny další vodiče do desky elektroniky. Na vodiče které se zapojují do svorkovnic nakrimpujeme zakončovací dutinky dutinky
17. Na stolek umístíme sklo a přichytíme ho svěrkami z pytlíku č. 39. Odpojíme konektory motorů z desky elektroniky. Teď můžeme pohybovat posuvy a nastavíme výšku stolku. Extruder nastavíme nad střed stolku. Otáčením os motorů svislé osy najedeme tryskou těsně nad sklo. Vyrobil jsem si "měrku" z tvrdého lesklého papíru a dojel tryskou tak, aby měrkou šlo mezi tryskou a sklem pohybovat ale musí být cítit že už je sevřená mezi sklem a tryskou. Pak najíždíme postupně do všech rohů stolku a nastavíme seřizovacími kolečky stejnou mezeru mezi tryskou a sklem.

18. Pokračovat budeme seřízením koncového spínače svislé osy. Moje papírová měrka má tloušťku 0,3mm takže v okamžiku kdy jsme nastavili stolek máme trysku cca 0,3mm nad sklem. A to je poloha ve které by měl koncový spínač vypnout. Povolíme šroub držáku mikrospínače a dojedeme mikrospínačem do takové polohy aby raménko mikrospínače dosedlo na dotykovou plochu posuvu Z. Šroub držáku mikrospínače utáhneme a nastavovacím šroubkem otáčíme až mikrospínač sepne. Otáčením os motorů svislého posuvu poodjedeme a opět najedeme na spínač abychom viděli jak spínač spíná a rozpíná. Spínač by měl zabránit dotyku trysky se sklem.
19. Vybalíme zdroj a připevníme ho zezadu na pravý svislý hranol. Já jsem k tomu použil poněkud nestylově kus Al plechu který jsem z boku přišrouboval ke zdroji šrouby se zápustnou hlavou a celý zdroj jsem pak přišrouboval šrouby M6 do matek které jsem při montáži portálu připravil do drážky v svislém profilu.


20. Natáhneme 2 tlusté dvojlinky od zdroje k napájecí svorkovnici na desce RAMPS. Na straně zdroje na konec dvojlinky nakrimpujeme vidličky pod šroubek a na straně RAMPS zakončovací dutinky. Vodiče jsou protažené středem zadního profilu. Bylo by možné rovněž natáhnout jen jednu dvojlinku a na koncích ji rozdělit. Takto mi to ale vycházelo lépe. Napájecí dvojlinky zatím do desky RAMPS nepřipojujeme.

21. Na zdroj připevníme velký ventilátor. K připevnění jsem použil stahovací pásky. Ventilátor umístíme tak aby chladil především feritová jádra. Spínací tranzistory chladí obal zdroje a navíc částečně i masa svislého hliníkového profilu. Později se ukázalo, že je zdroj za provozu naprosto studený. Vývody od ventilátoru patřičně zkrátíme, opatříme zakončovacími dutinkami a připojíme do posledních volných svorek na zdroji. Žlutý drát určený ke snímání otáček ventilátoru nepotřebujeme a proto ho ustřihneme úplně aby nám nepřekážel. Potřebná orientace ventilátoru je naznačena piktogramy na plastovém těle ventilátoru. Ventilátor má tlačit vzduch dovnitř zdroje. Protože je výkon ventilátoru zbytečně vysoký snížil jsem jeho otáčky a hlučnost vložením odporu cca 18Ω/0,25W do přívodu k ventilátoru. Úbytek na tomto odporu je cca 2V.


22. Do napájecích svorek zdroje připojíme Flexo šňůru 220V a zapojíme ji do zásuvky. Na zatím nepřipojených napájecích vodičích na straně RAMPS ověříme že zdroj dává skutečně 12V. Můžeme zkusit zdroj i zatížit např. automobilní žárovkou.
23. Pokud je vše v pořádku vypneme napájecí zdroj a můžeme připojit napájecí dvojlinky do svorkovnice na desce RAMPS. Teď je vhodná příležitost ještě jednou překontrolovat připojení všech kabelů do desky RAMPS. Hlavně zkontrolujte polaritu připojených zařízení a u motorů správnou orientaci připojení konektorů.


24. Zapneme napájení. Měla by se rozsvítit zelená LED dioda na Arduinu. Dále by se měl rozběhnout ventilátorek chlazení extruderu. Pokud by se nerozběhnul změňte polaritu jeho napájecího napětí otočením konektoru. Zkontrolujte že se točí ventilátor zdroje a tlačí vzduch dovnitř zdroje.
25. Změříme napětí na běžcích trimrů všech driverů. Nastavte je na 0,5V proti zemi. Během nastavování se nesmí hýbat s motory ! Zem nalezneme třeba na konektoru vlevo od resetovacího tlačítka - pin nejblíže k okraji desky.

Tím máme hotovou elektrickou výbavu tiskárny a můžeme se začít věnovat jejímu rozběhnutí. Tomu se budu věnovat ve třetím dílu tohoto seriálu.

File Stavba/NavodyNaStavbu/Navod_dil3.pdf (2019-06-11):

## Postup stavby 3D tiskárny Rebel 2

Martin Čihák – OK1UGA
Díl třetí – Oživení .

V tomto díle seriálu zprovozníme tiskárnu a SW vybavení potřebné pro její provoz. Budu popisovat instalaci na svém PC se systémem Windows 7 64 bit. Na jiných systémech to bude podobné ale nemusí to probíhat stejně.

1. První kroky můžeme udělat se samotnou deskou Arduina ještě před tím než máme sestavenou tiskárnu. Samozřejmě je to možné i na sestavené tiskárně. Jako první krok musíme nainstalovat ovladače. Připojíme Arduino USB kabelem k PC. Systém by měl nalézt neznámé zařízení.


2. Stáhneme vývojové prostředí k Arduinu z adresy http://arduino.cc/en/Main/Software . Nejlepší je stáhnout ho v komprimovaném tvaru bez instalátoru ale na uvedené adrese je i vývojové prostředí s instalátorem. Stažené vývojové prostředí rozbalíme do vhodného adresáře.
3. Klikneme pravým tlačítkem na Neznámé zařízení a zvolíme vlastnosti. V následujícím okně zvolíme aktualizovat ovladač. K tomu potřebujeme administrátorská práva. Pokud je


pod naším účtem nemáme systém si vyžádá jméno a heslo administrátora.

4. Stískneme tlačítko aktualizovat. Vybereme vyhledat ovladač v počítači a najdeme adresář kam jsme rozbalili prostředí arduina. Přejdeme do podadresáře drivers.

5. Potvrdíme výběr stisknutím OK. Nevybírejte FTDI USB Drivers. Stiskněte další a spustí se instalace ovladačů Arduina.


6. Potvrďte instalaci a tím se ovladače Arduina nainstalují. Ve správci zařízení teď vidíme nové zařízení Arduino Mega 2560 s přiřazením COM portu (v mém případě COM20).


7. Tím máme nainstalované ovladače pro Arduino. Další instalaci a oživování již budeme provádět s hotovou tiskárnou. Existuje víc různých SW pro obsluhu 3D tiskáren. Já se budu věnovat programovému vybavení Repetier a Slicr3 které jsou patrně nejrozšířenější. Začneme stažením SW na stránce http://www.repetier.com/download/ . Vyberte svůj operační systém a přejdete na stránku kde můžete autorům programu věnovat nějaký finanční obnos. Vzhledem k náročnosti programu a velkému množství práce která na něm musela být odvedena si to autoři zaslouží. Nicméně dole je i nenápadný odkaz na stažení bez platby. Stažená instalace obsahuje i program Slicr3 takže ho nemusíme stahovat samostatně.
8. Spustíme stažený instalační program. Instalace probíhá standardním způsobem. Vyberte adresář kam se má program nainstalovat jinak všechny volby můžete ponechat tak jak jsou. Na konci můžeme nechat program spustit. Obrázek ukazuje program spuštěný hned po instalaci. Je tam přímo vložený nějaký objekt abychom si měli hned s čím hrát :-).


9. Zapneme tiskárnu a připojíme ji k PC. Ve správci zařízení si pro jistotu zkontrolujeme port na kterém tiskármu máme. Někdy se totiž stává že se při připojení na jiný USB slot změní číslo portu. Já mám tiskárnu stále na portu 20. V menu vybereme položku Config a vybereme v položce Language češtinu - tedy pokud Vám jiný jazyk nevyhovuje lépe. Pak vybereme položku nastavení tiskárny a na kartě Připojení vybereme COM port na kterém máme tiskárnu. Já tedy vybírám COM20. Ostatní volby prozatím ponecháme beze změny. Potvrdíme tlačítkem OK a vrátíme se zpět do Repetieru.


10. Vlevo nahoře stiskneme velké červené tlačítko Připojit. Pokud je vše v pořádku tlačítko zezelená a na spodním stavovém řádku se začnou vypisovat informace o teplotách. Zatím je tiskárna v klidu, takže jsou teploty tam pokojové teploty. Můžeme tyto teploty překontrolovat bezkontaktním teploměrem. U mě se teploty lišily o méně než 0,5°C.
11. V programu na pravé straně zvolíme záložku Manual Control (program není přeložen celý).


12. Zde máme možnost ovládat ručně jednotlivá elektrická zařízení tiskárny a otestovat tak jejich funkčnost. Vyzkoušíme opatrně všechny 3 posuvy a parkování os X, Y i Z na koncové spínače. To se dělá pomocí tlačítek Z, Y a Z v domečku. Tím se kalibrují nulové polohy jednotlivých posuvů tiskárny. Po stisku tlačítka tiskárna najede posuvem na příslušný koncový spínač, vrátí se o kousek zpět a najede na něj ještě jednou pomaleji. Tak přesně nalezne nulovou souřadnici každého posuvu. Pozor ale na kalibraci vertikální osy. Při tom musí být tryska mimo sklo, protože během kalibrace najede kousek pod nulovou polohu a narazila by na sklo. Proto je vhodné udělat kalibraci osy X, ponechat trysku v nulové poloze a pak provést kalibraci ozy Z.
13. Dále ověříme rovnoběžnost vodících tyčí osy X se základnou. Postup je jednoduchý. Vyjedeme s vertikálním posuvem co nejvíce nahoru. Vložíme pravítko nebo nějakou tyč mezi posuvovou tyč osy X a horní profil portálu co nejblíže k jedné straně tiskárny.
Otáčením závitové tyče
nastavíme vodorovnou polohu vloženého pravítka. Pak
pravítko přesuneme na druhou stranu tiskárny a druhým
motorem nastavíme rovněž
vodorovnou polohu pravítka. Tím jsme zajistili
rovnoběžnost osy X se
základnou tiskárny.



14. Pokud jsme změnili nastavení os motorů vůči sobě musíme teď znovu provést výškové seřízení stolku a rovněž opravit nastavení koncového spínače vertikální osy.
15. Nyní můžeme vyzkoušet ovládání ventilátoru a topení extruderu a stolku. Motor extruderu se zatím neroztočí protože je jeho funkce blokována při nízké teplotě. Proto nejprve musíme vytopit extruder a pak teprve lze otestovat jeho motor.
16. Následovat by mělo nastavení oblasti tisku a dalších důležitých parametrů tiskárny. To ale již nebude předmětem tohoto popisu protože jsem si vzal za úkol popsat sestavení tiskárny. Naše tiskárna je hotová a můžeme ji začít používat. Tím moje práce končí. Necítím se dostatečně fundovaný k tomu abych popisoval práci s programem repetier a vlastní 3D tisk. To je stále do značné míry technologie v prvních stádiích vývoje a pro úspěšný tisk chce to určité zkušenosti které v této chvíli nemám.

17. První pokus o tisk u mě dopadl docela tragicky protože tiskárna dávala málo plastu.


Pak jsem použil průvodce pro nastavení Sliceru. Po zodpovězení pár jednoduchých otázek na vlastnosti tiskárny se vše nastavilo jak má a tiskárna začala tisknout správně. Na obrázku je vidět první a druhý pokus o tisk.
18. Další drobný problém byl v tom, že jsem měl nastavený koncový spínač svislé osy příliš vysoko a tak jsem ho nastavil metodou Pokus-Omyl až se první vrstva tiskla jak má. Je nutné aby u první vrstvy tryska rozmáčkla plast na sklo. Proto se taky ve vlastnostech tiskárny nastavuje tloušťka první vrstvy menší než u ostatních vrstev.
19. Při oživování tiskárny mě trochu potrápil problém kdy motory točily špatným směrem a zcela zmateně měnily směr otáčení. Někdy se úplně zastavily a jen jemně pískaly. Pokud by se Vám podobná závada projevila jde o vadný driver. Žádný jiný problém kromě těch které jsem si sám vyrobil jsem nezaznamenal.


Přeji všem aby se Vám podařilo tiskárnu postavit a dovést stavbu ke zdárnému konci. Pokud Vám můj popis k tomuto cíli dopomohl jsem rád.

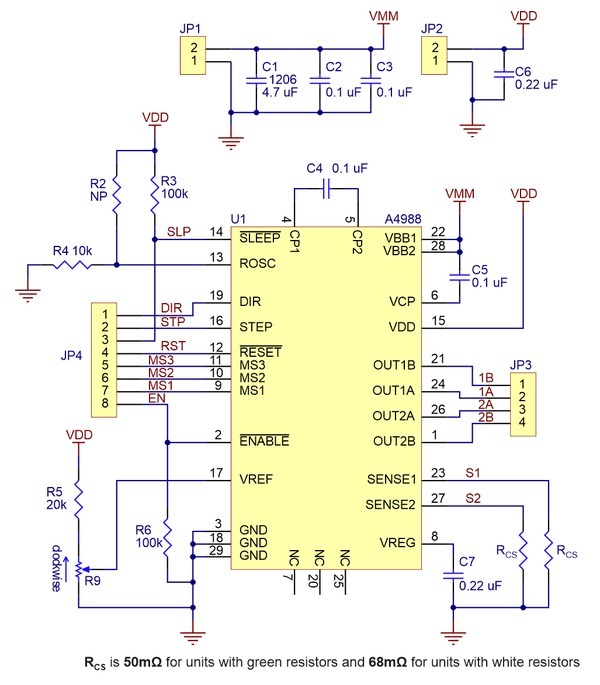
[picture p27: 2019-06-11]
Datasheet/eletronika/pololudriver_schematic.jpg

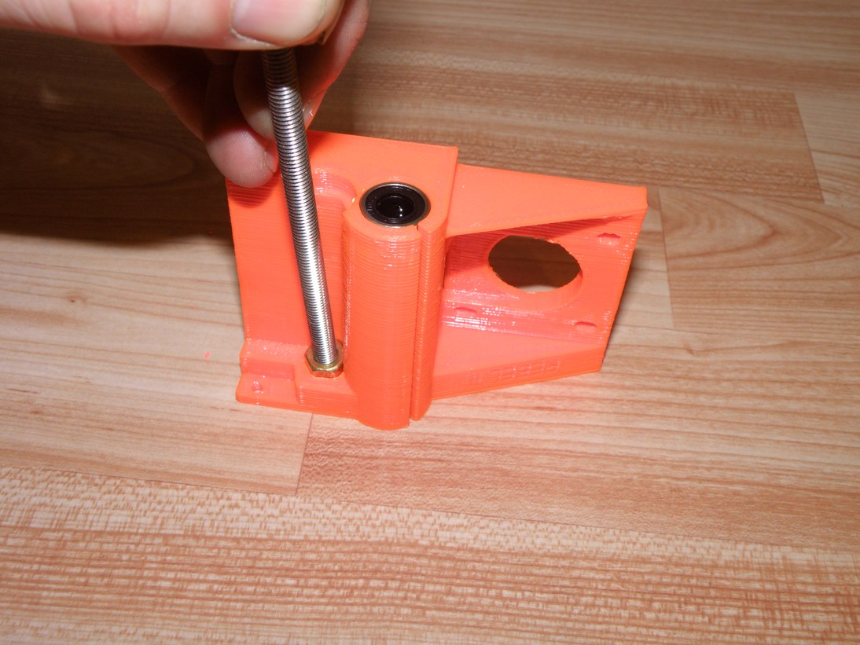
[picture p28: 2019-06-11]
Stavba/NavodyNaStavbu/rebel2-foto-montaz/026-nalisovani matky Z osy.JPG

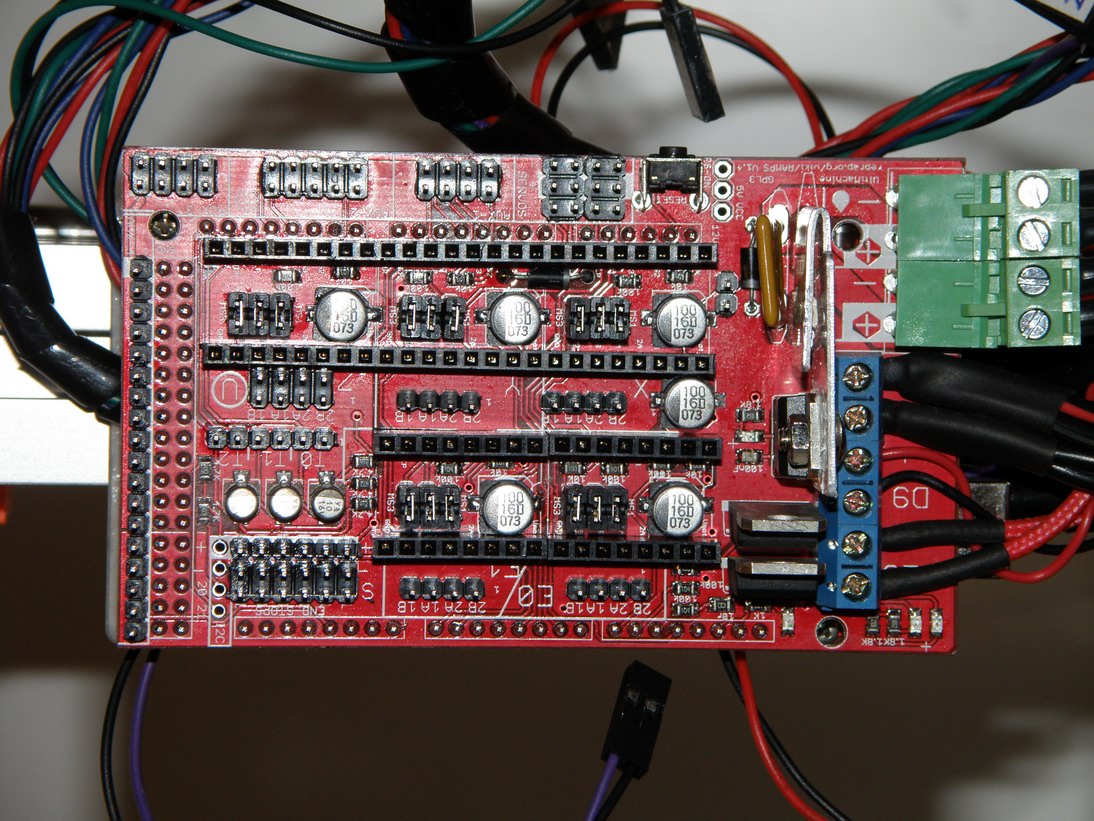
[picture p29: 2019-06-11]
Stavba/NavodyNaStavbu/rebel2-foto-montaz/101-krokovani.JPG

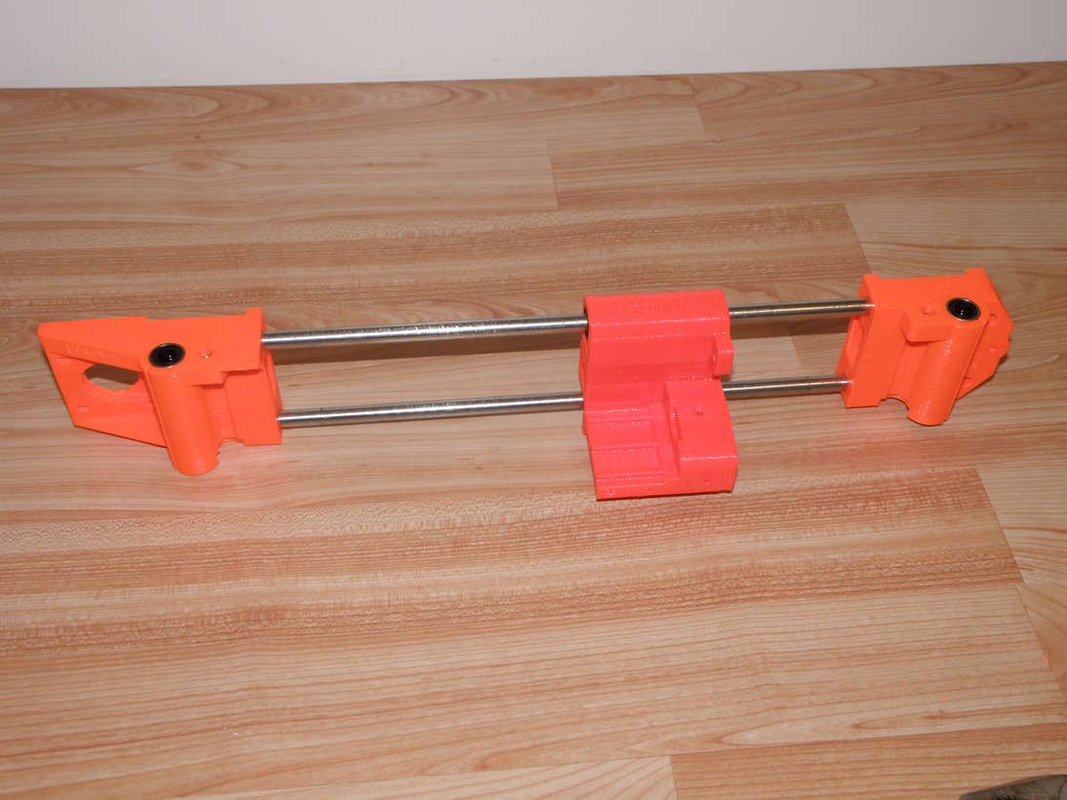
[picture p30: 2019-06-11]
Stavba/NavodyNaStavbu/rebel2-foto-montaz/031-hotova rampa X.JPG

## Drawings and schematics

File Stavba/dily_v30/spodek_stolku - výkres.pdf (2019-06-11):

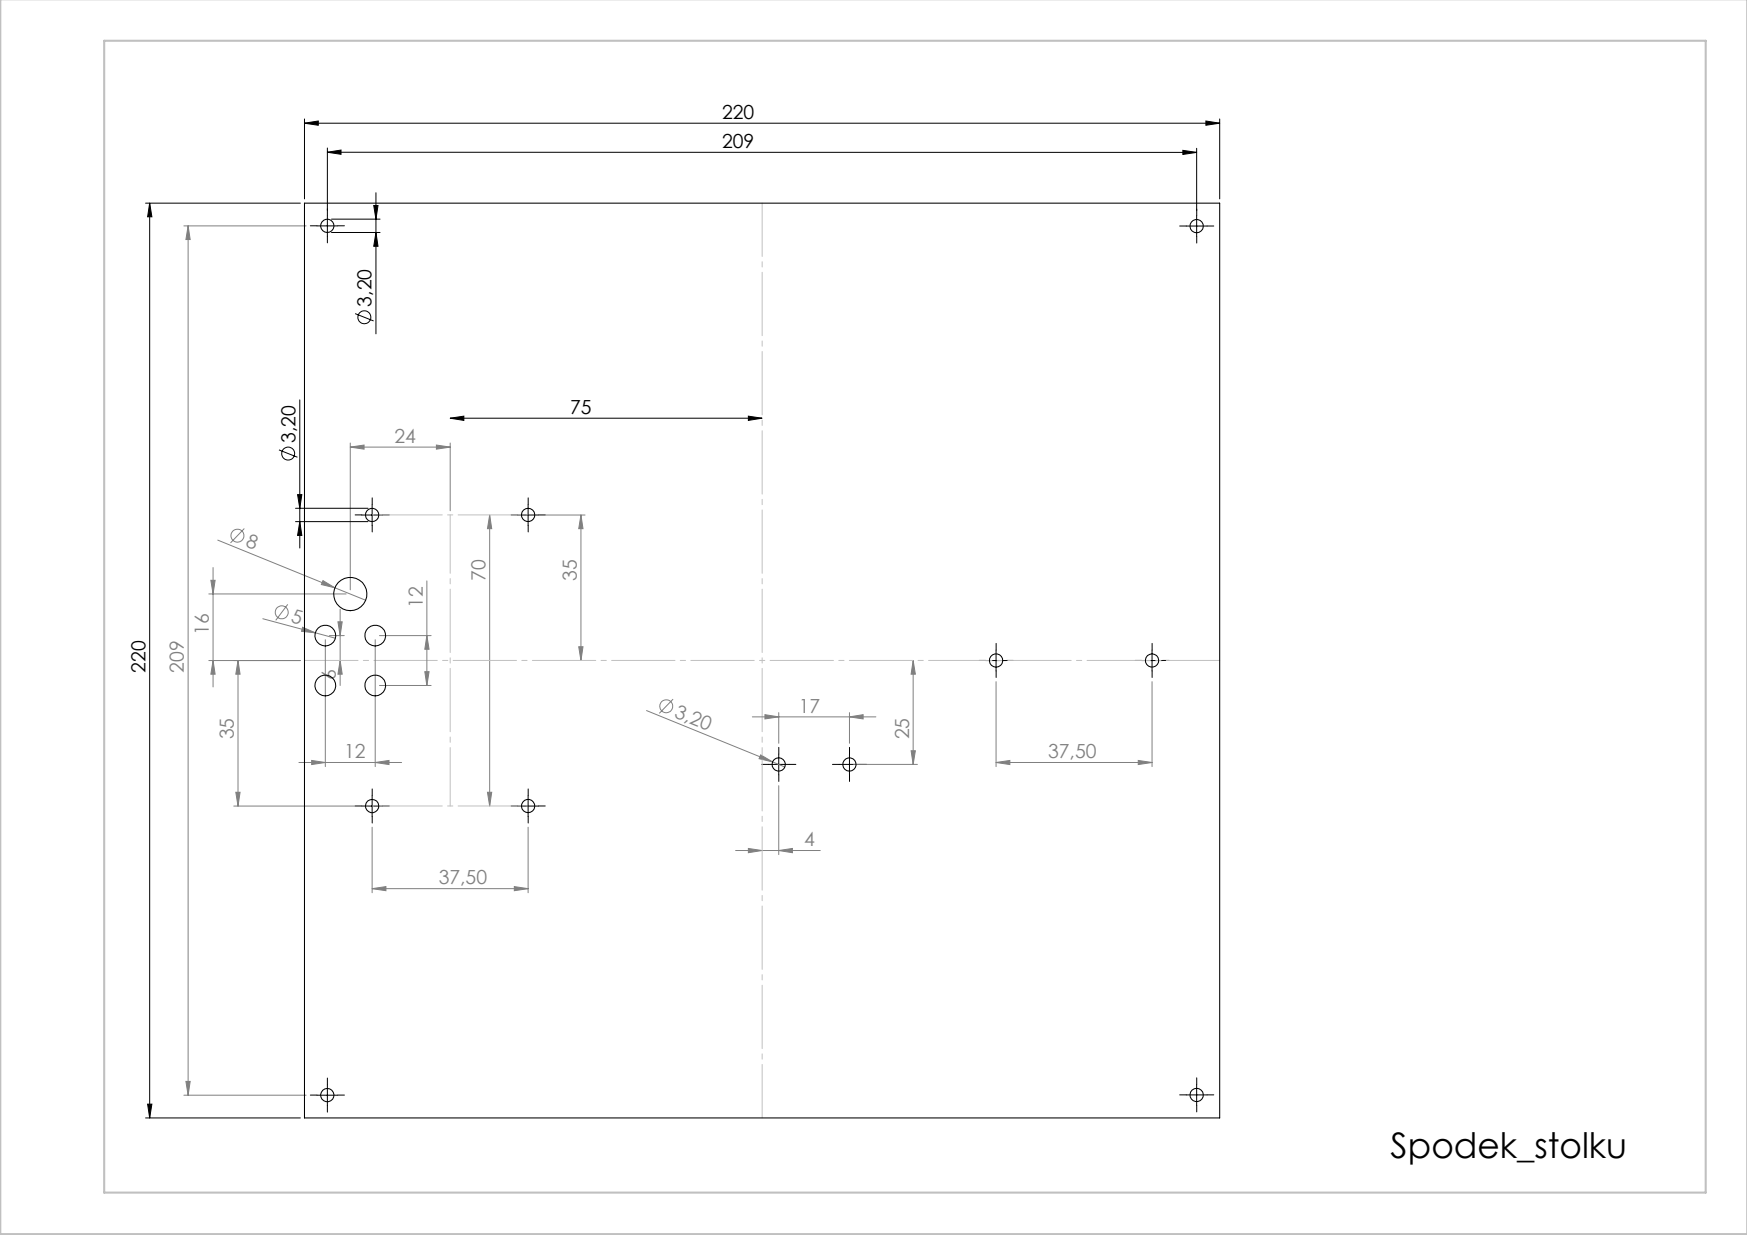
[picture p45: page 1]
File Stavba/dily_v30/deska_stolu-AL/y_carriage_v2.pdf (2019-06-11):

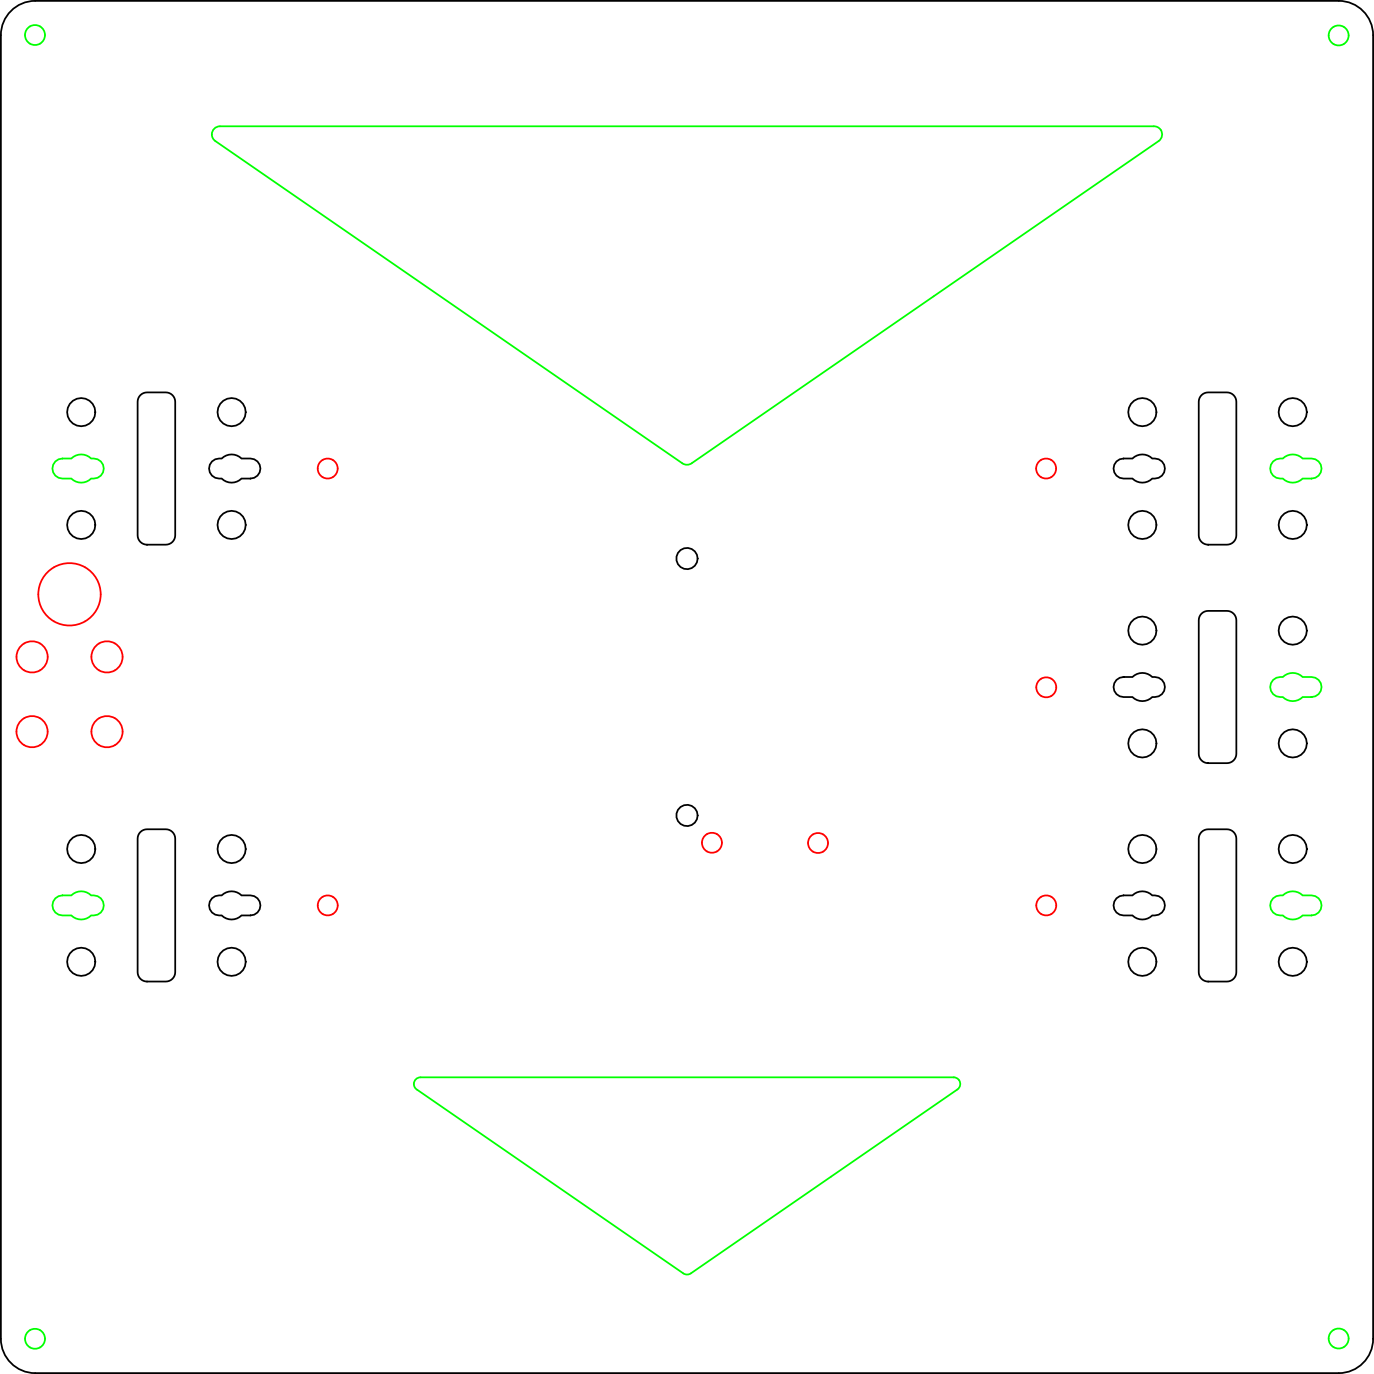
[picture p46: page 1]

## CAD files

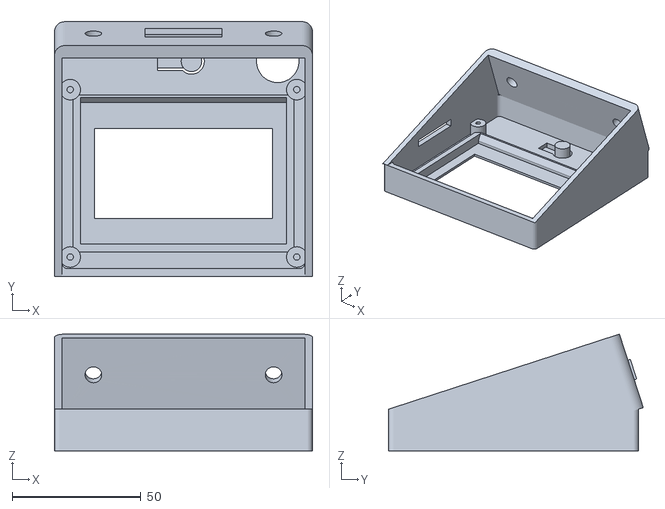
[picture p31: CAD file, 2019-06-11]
Stavba/dily_v30/tistene_dily_rebel_ii_v30_jrc/Full_g_LCD_vrchni.stl
100.2 x 98.9 x 45.3

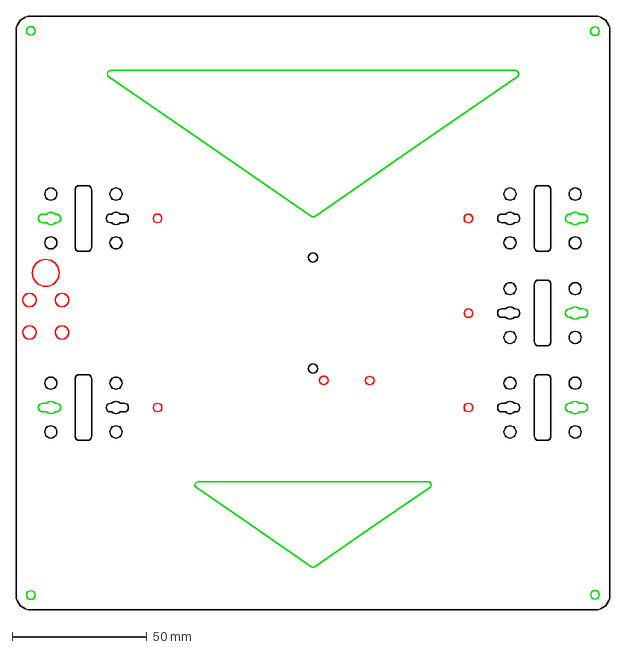
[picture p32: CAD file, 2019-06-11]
Stavba/dily_v30/deska_stolu-AL/y_carriage_v2.dxf
220.0 x 220.0 mm

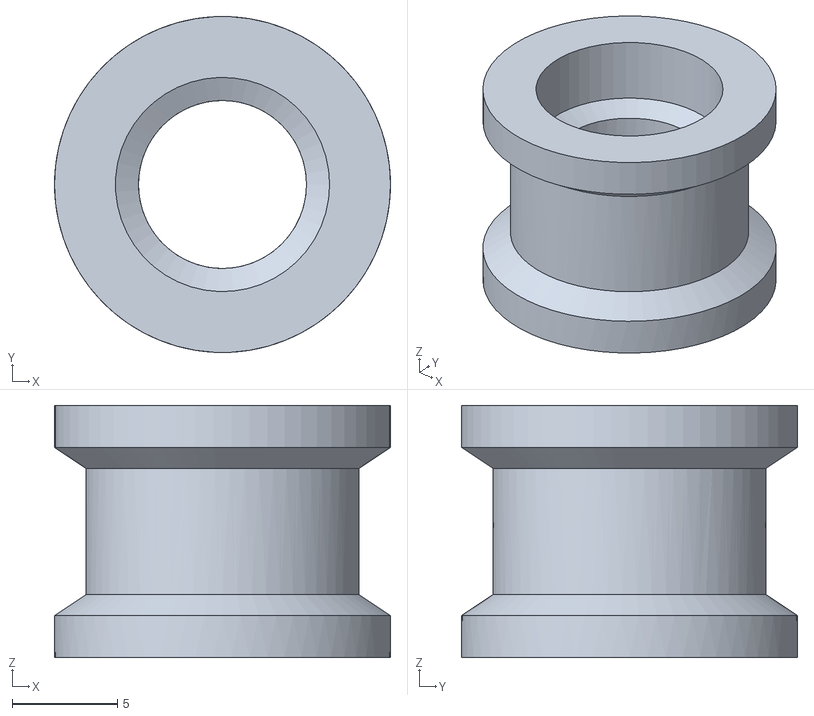
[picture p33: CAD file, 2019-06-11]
Stavba/dily_v30/Stl_Tisk_v30/All/Remenice_T2.5_0z-2ks.STL
16.0 x 16.0 x 12.0

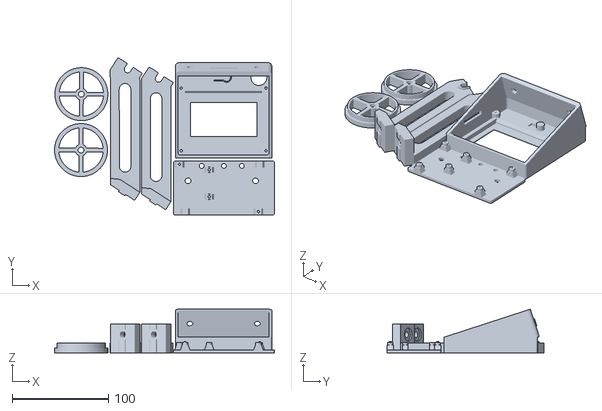
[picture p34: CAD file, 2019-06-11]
Stavba/dily_v30/Stl_Tisk_v30/Sestava_jakub/Sestava_J6_white.stl
228.2 x 163.0 x 45.3

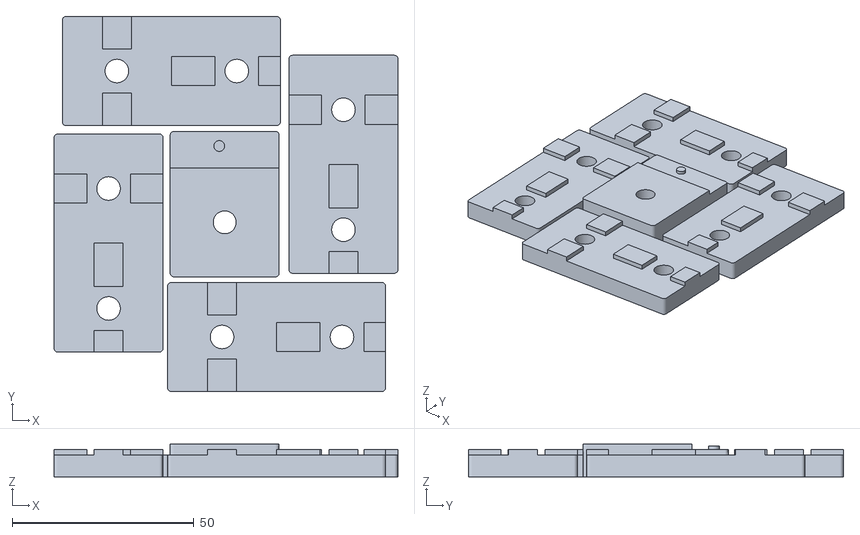
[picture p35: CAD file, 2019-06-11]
Stavba/dily_v30/Stl_Tisk_v30/Sestavy_STL/Sestava10.stl
94.6 x 103.2 x 9.00

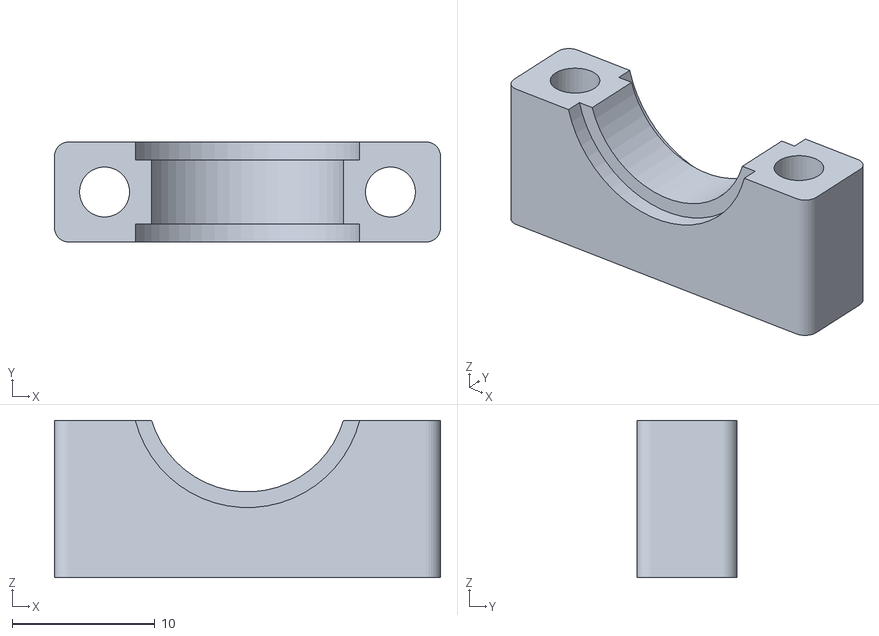
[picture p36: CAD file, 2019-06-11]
Stavba/dily_v30/Stl_Tisk_v30/Tisk01/Trmen_holderu_trysky-1ks.STL
27.0 x 7.00 x 11.0

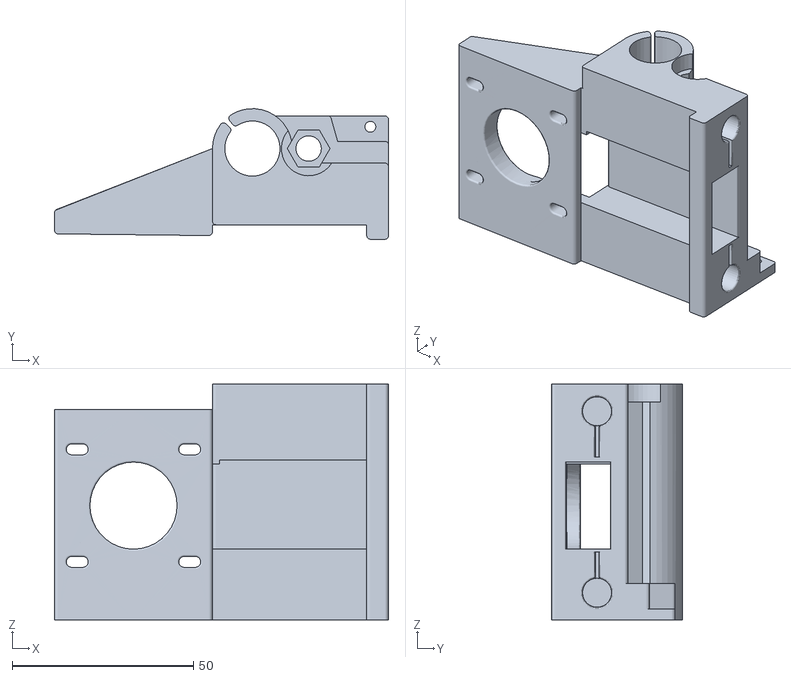
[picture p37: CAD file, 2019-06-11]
Stavba/dily_v30/Stl_Tisk_v30/Tisk02/Pojezd_Z_levy_v30-1ks.stl
92.0 x 36.0 x 65.0

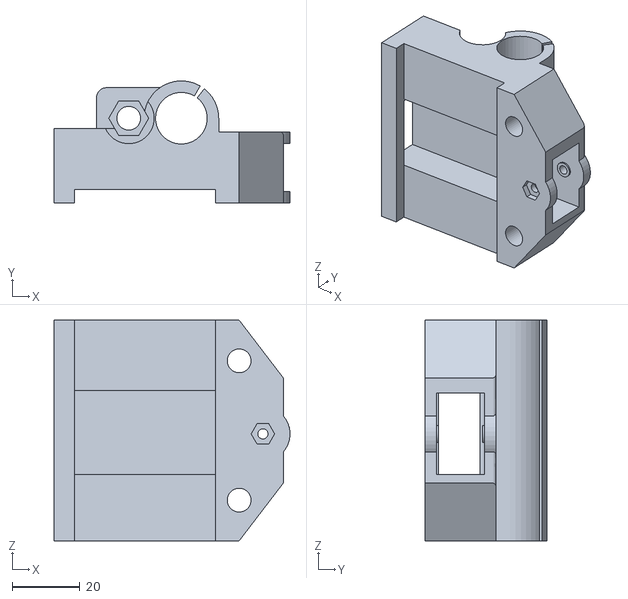
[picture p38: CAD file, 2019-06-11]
Stavba/dily_v30/Stl_Tisk_v30/Tisk03/Pojezd_Z_pravy-1ks.STL
69.5 x 36.0 x 65.0

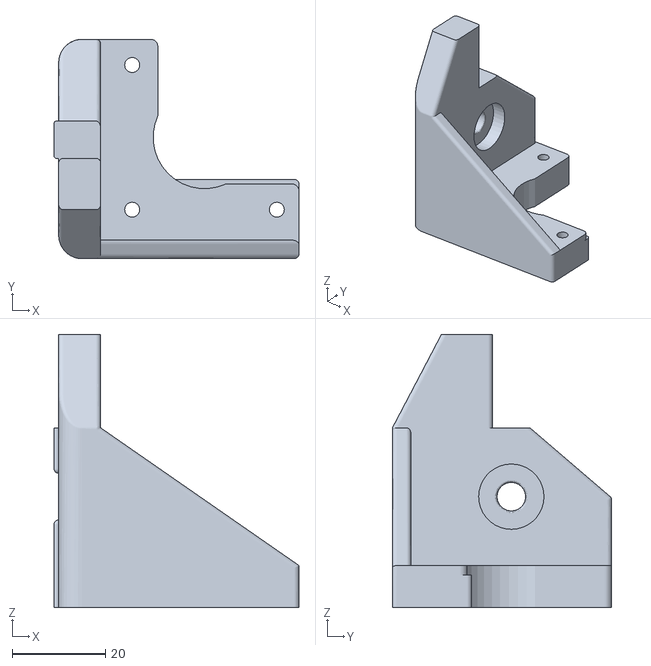
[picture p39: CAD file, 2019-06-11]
Stavba/dily_v30/Stl_Tisk_v30/Tisk04/Uchyceni_motoru_Z_pravy_v30-1ks.STL
52.5 x 47.0 x 58.5

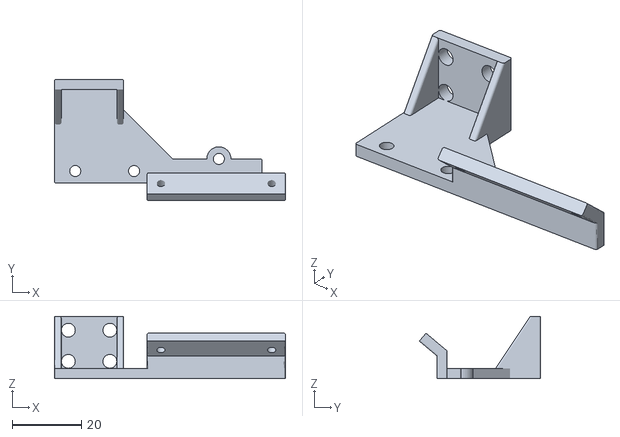
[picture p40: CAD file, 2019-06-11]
Stavba/dily_v30/Stl_Tisk_v30/Tisk05/Drzak_ventilatoru_a_kabelaze_extruderu-1ks.STL
66.8 x 35.1 x 18.0

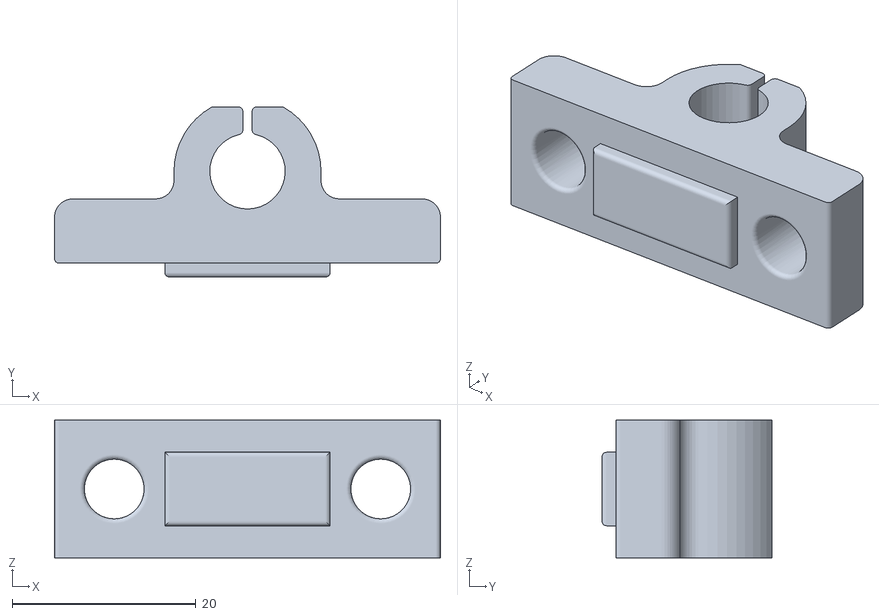
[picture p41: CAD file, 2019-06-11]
Stavba/dily_v30/Stl_Tisk_v30/Tisk06/UchyceniTyce8mm_v30-4ks.STL
42.0 x 18.5 x 15.0

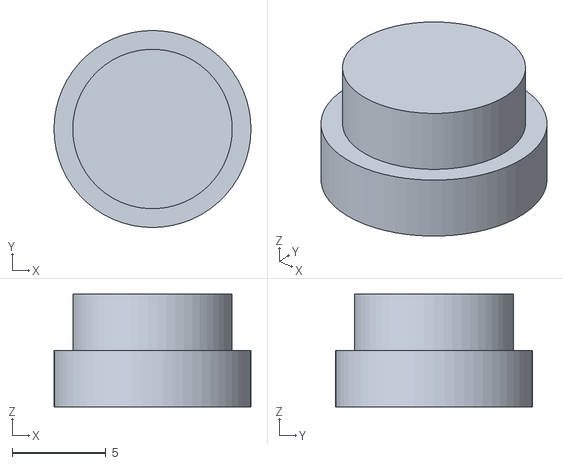
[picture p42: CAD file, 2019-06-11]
Stavba/dily_v30/Stl_Tisk_v30/Tisk07/Drzak_packy_extruderu_dil2-1ks.STL
10.5 x 10.5 x 6.00

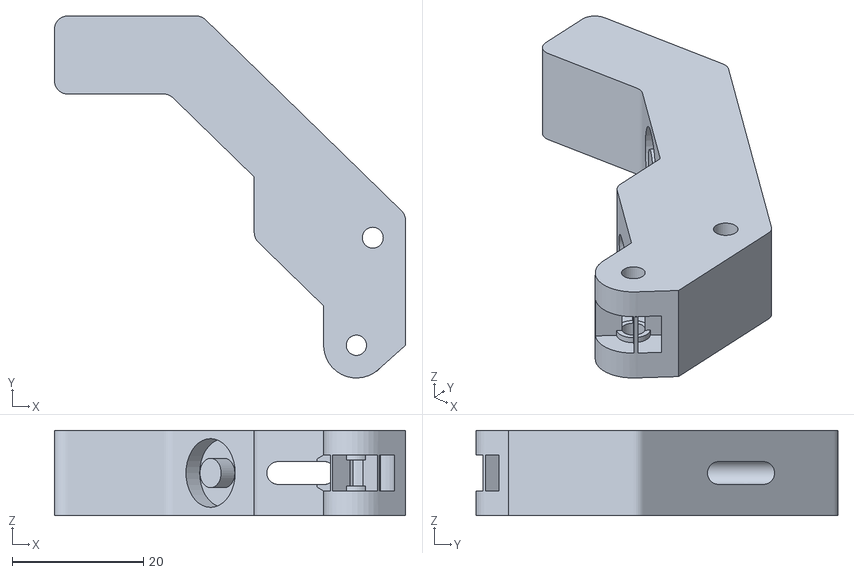
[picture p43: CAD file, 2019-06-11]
Stavba/dily_v30/Stl_Tisk_v30/Tisk08/Packa_extruderu-1ks.STL
53.6 x 55.2 x 13.0

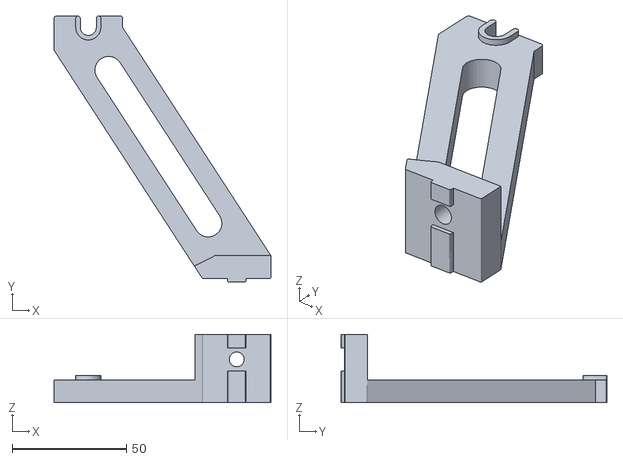
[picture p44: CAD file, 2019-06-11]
Stavba/dily_v30/Stl_Tisk_v30/Tisk09/Drzak_spulky_Filamentu_pravy_v30-1ks.STL
95.0 x 116.5 x 30.0

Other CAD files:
Stavba/dily_v30/Stl_Tisk_v30/Tisk10/Vazba_rohu_v30_4ks.STL
Stavba/dily_v30/Stl_Tisk_v30/Tisk11/Vazba_rohu_v30_spodni_LP_2ks.STL
Stavba/dily_v30/Stl_Tisk_v30/Tisk12/Drzak_Mega.STL
Stavba/dily_v30/tistene_dily_rebel_ii_v30_jrc/Fan_mount_V5_4.STL
Stavba/dily_v30/Stl_Tisk_v30/All/ABS_distanc_stolku-4ks.STL
Stavba/dily_v30/Stl_Tisk_v30/All/Drzak_LM8UU-4ks.STL
Stavba/dily_v30/Stl_Tisk_v30/All/Drzak_Mega.STL
Stavba/dily_v30/Stl_Tisk_v30/All/Drzak_koncaku_Y_v30-1ks.STL
Stavba/dily_v30/Stl_Tisk_v30/All/Drzak_koncaku_Z_v30-1ks.STL
Stavba/dily_v30/Stl_Tisk_v30/All/Drzak_motoru_Y_v30-1ks.STL
Stavba/dily_v30/Stl_Tisk_v30/All/Drzak_packy_extruderu-dil1-1ks.STL
Stavba/dily_v30/Stl_Tisk_v30/All/Drzak_remene_Y-2ks.STL
Stavba/dily_v30/Stl_Tisk_v30/All/Drzak_remene_Y_zaklad-1ks.STL
Stavba/dily_v30/Stl_Tisk_v30/All/Drzak_remenice_Y-1ks.STL
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
